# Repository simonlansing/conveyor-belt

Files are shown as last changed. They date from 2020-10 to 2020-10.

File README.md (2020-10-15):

# Miniature Conveyor Belt 

Miniature conveyor belt for simulation and having fun working with sensors and actuators, all controllable with Raspberry Pi. All sensors and actuators of the conveyor belt are connected to the GPIO pins of the Raspberry Pi via a separate circuit board. The board also contains a motor driver, a push button and three LEDs.

As simulation software [Node-RED](https://nodered.org/) is used locally on the Raspberry Pi. Based on this, the sensors and actuators could also be mapped as device shadows in the AWS IoT platform (Software follows :smile:).

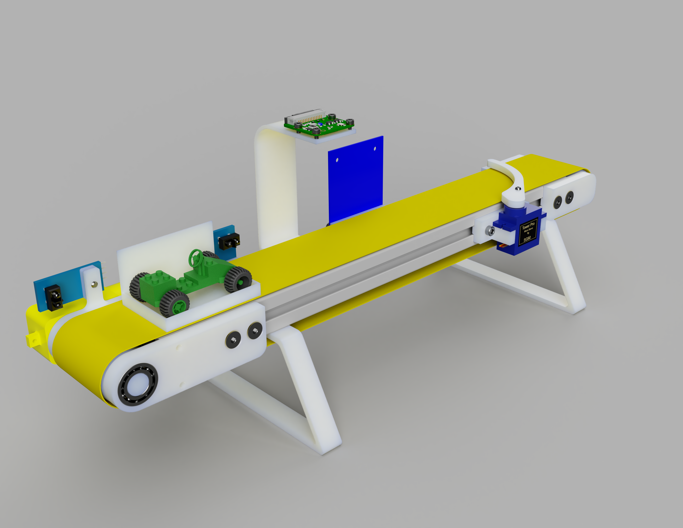
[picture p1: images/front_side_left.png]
image of front side front side

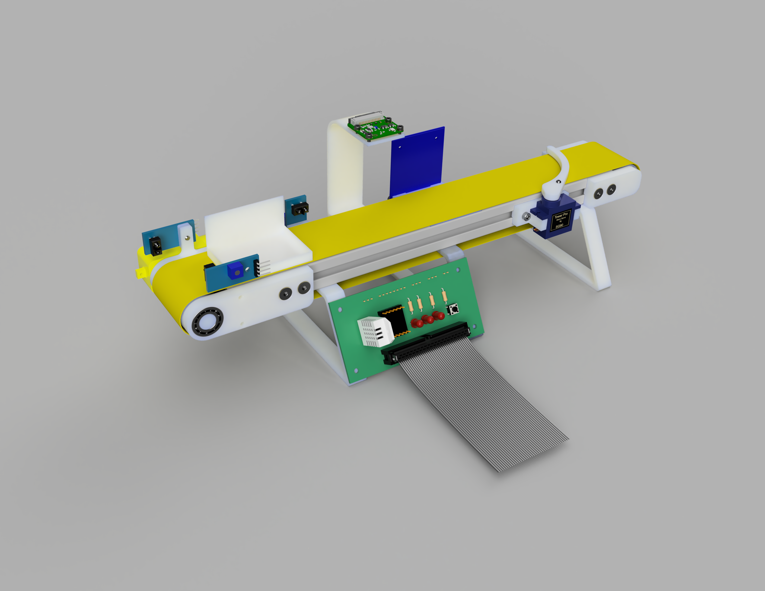
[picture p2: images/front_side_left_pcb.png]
image of front side with PCB front side with PCB

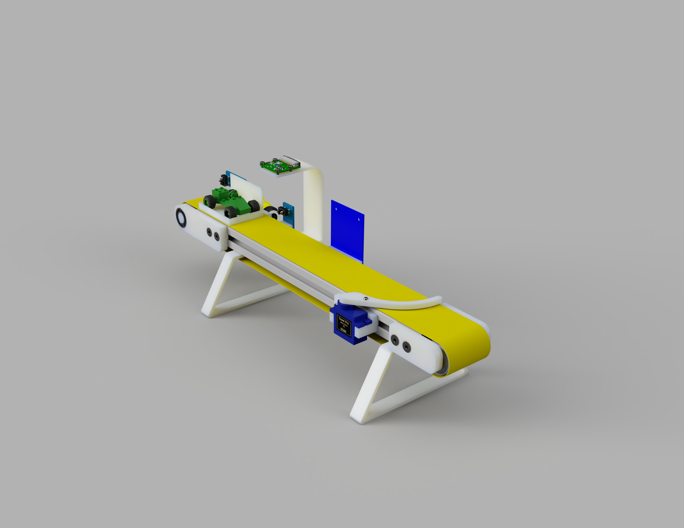
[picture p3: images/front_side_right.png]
image of front side 2 front side from other angle

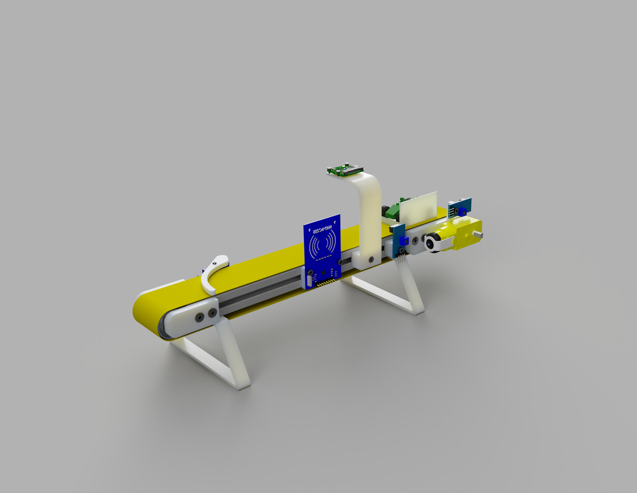
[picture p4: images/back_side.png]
image of back side back side


## Components

The following components were used and can be screwed directly to the 3D-printed parts.

### Hardware

| No. | Name | Quantity  | Notes |
| :-: | :--- | :---: | :--- |
| 1 | RFID reader RC522 | 1 | |
| 2 | IR photoelectric switch barrier TRCT5000 | 1-3 | |
| 3 | Servo motor SG90 | 1 | |
| 4 | Motor driver DRV8833 | 1 | |
| 5 | TT motor DC3V-6V | 1 | |
| 6 | Raspberry Pi Camera Module | 1 | |
| 7 | Raspberry Pi 3/4 | 1 | |
| 8 | Ball bearing 608 2RS 8x22x7 mm | 2 | deflection roll |
| 9 | Ball bearing 6800 zz 10x19x5 | 2 | drive roll |
| 10  | Aluminium profile 20mm x 40mm x 290mm | 1 | |
| 11  | Elastic band | 1 | |
| 12  | LEDs | 3 | |
| 13  | Resistors for LEDs | 3 | |
| 14  | Push button | 3 | see PCB |

### Screws

| No. | Name | Quantity  | Notes |
| :-: | :--- | :---: | :--- |
| 1 | M3 x 8 countersunk screw | 4 | |
| 2 | M3 x 10 countersunk screw | 3 | |
| 3 | M3 x 12 countersunk screw | 6 | |
| 4 | M4 x 10 countersunk screw | 24 | |
| 5 | M4 x 12 countersunk screw | 24 | |
| 6 | M3 x 5 flat headed screw | 6 | |
| 7 | M3 x 10 flat headed screw | 6 | |
| 8 | M3 x 12 flat headed screw | 6 | |
| 9 | M3 x 18 flat headed screw | 13 | |
| 10  | M3 x 25 flat headed screw | 6 | |
| 11  | M2 spacer | 6 | |

### 3D printed parts

| No. | Name | Quantity  | Notes |
| :-: | :--- | :---: | :--- |
| 1 | box | 1 | |
| 2 | camera mount | 1 | |
| 3 | deflection roll | 1 | |
| 4 | deflection roll mount | 1 | |
| 5 | deflection roll mount mirrored  | 1 | |
| 6 | drive roll | 1 | |
| 7 | foot | 2 | |
| 8 | IR sensor mount | 1-2 | one servo is mounted on the motor |
| 9 | motor mount | 1 | |
| 10  | motor mount mirrored | 1 | |
| 11  | servo lever | 1 | |
| 12  | servo mount | 1 | |

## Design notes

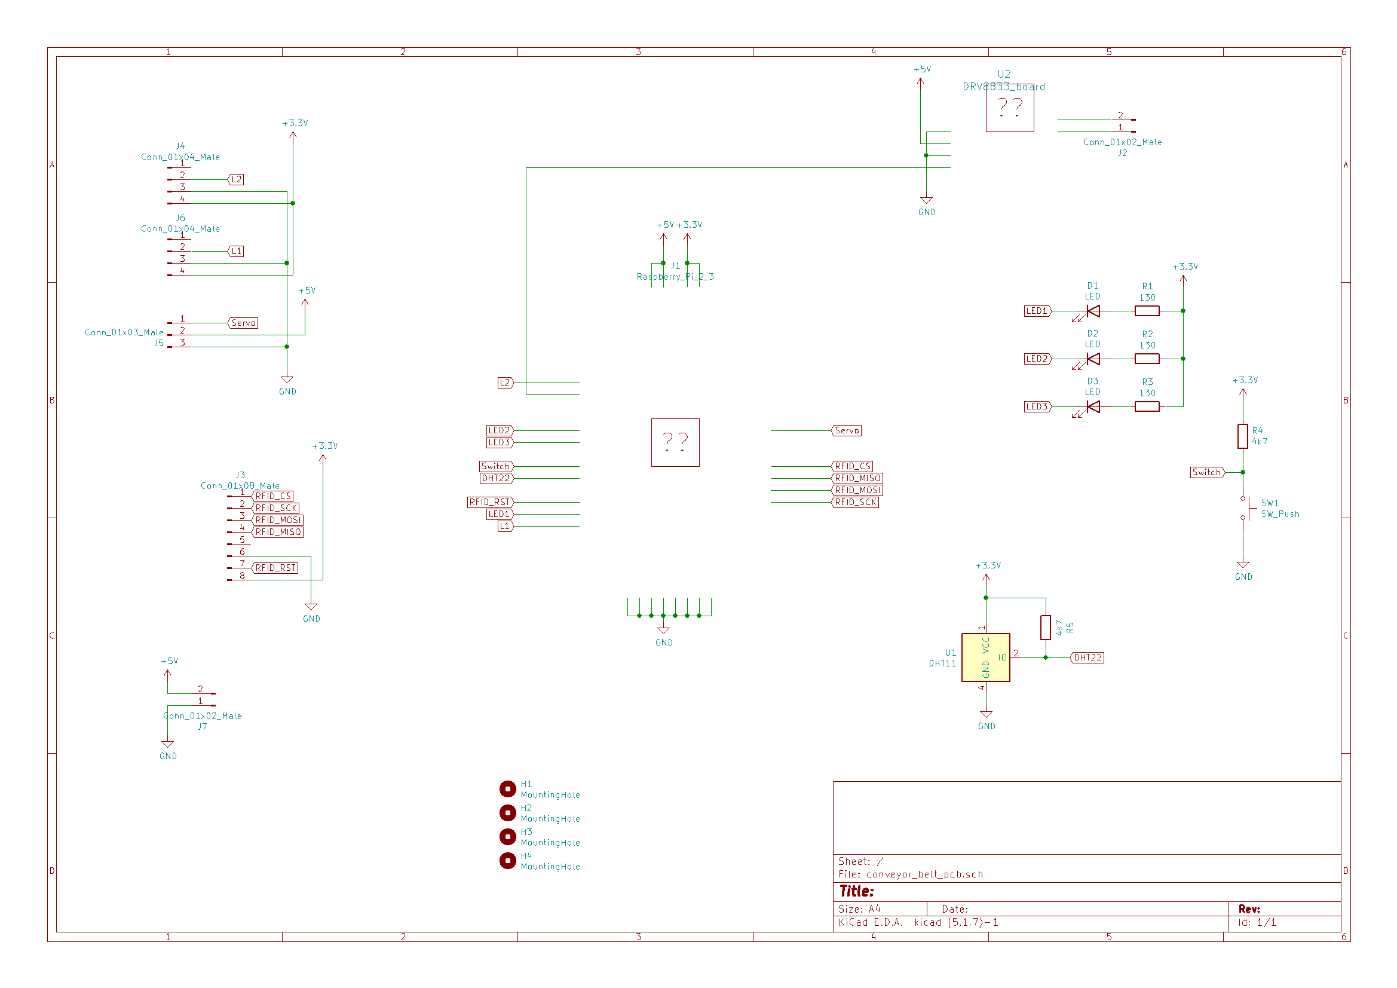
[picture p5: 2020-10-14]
images/circuit_diagram.png

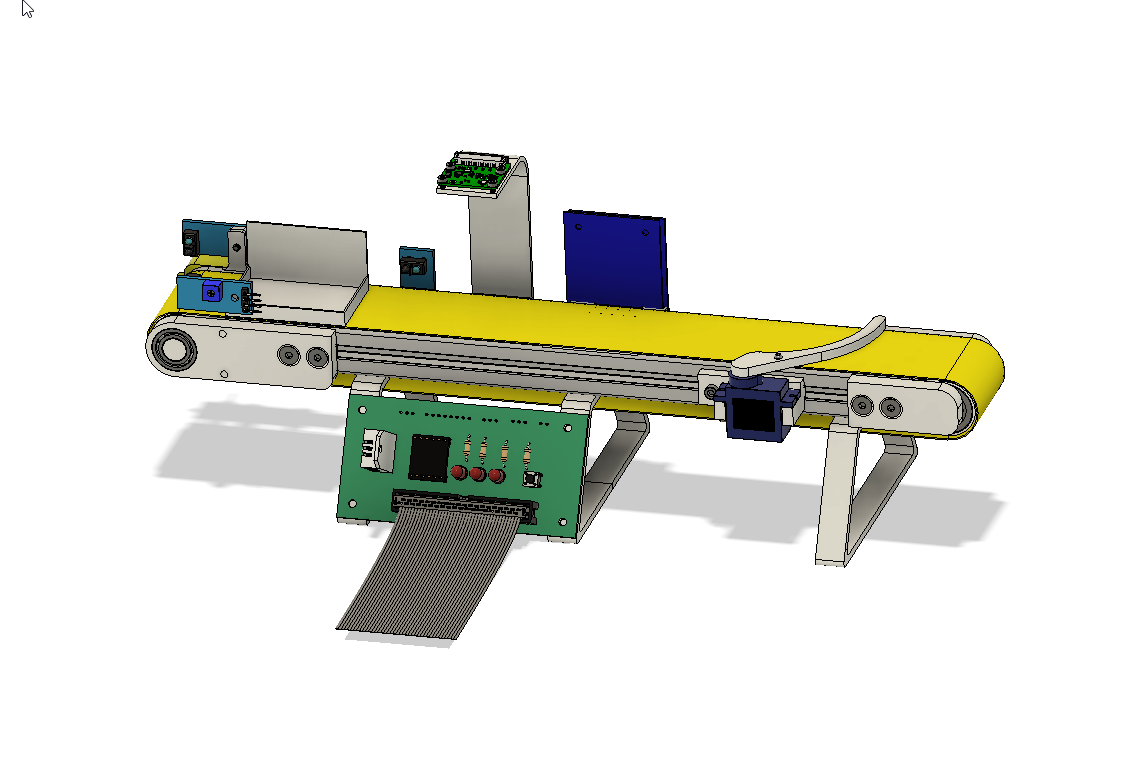
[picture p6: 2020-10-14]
images/front_pcb.png

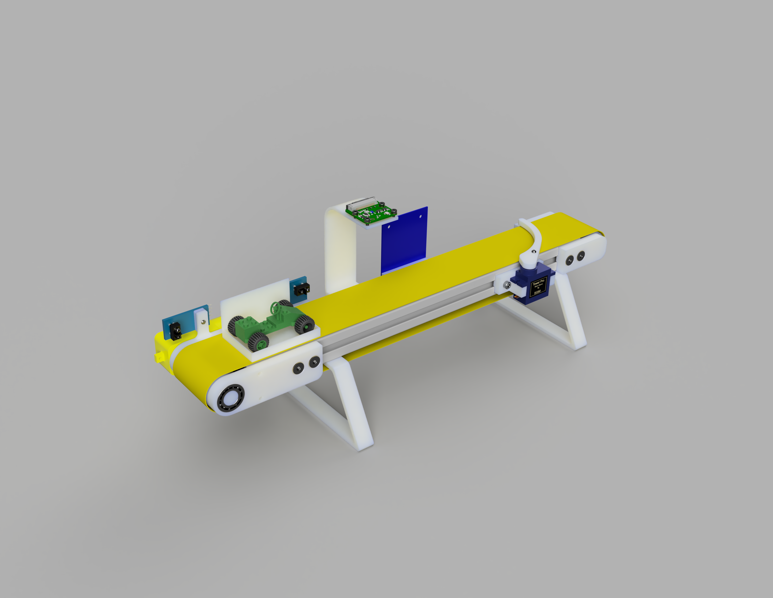
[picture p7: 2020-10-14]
images/front_side_left_2.png

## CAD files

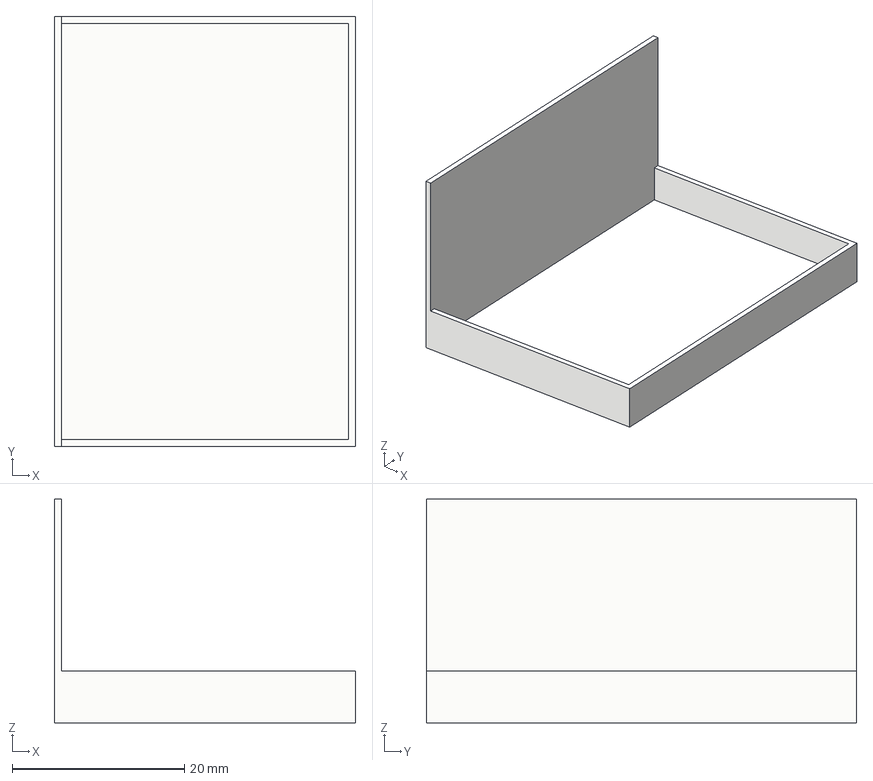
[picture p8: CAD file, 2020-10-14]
3d parts/box.step
35.0 x 50.0 x 26.0 mm

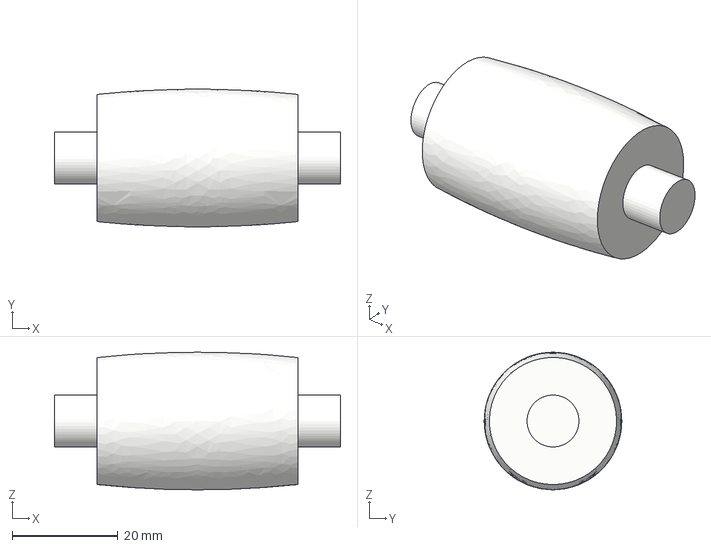
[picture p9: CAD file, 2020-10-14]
3d parts/drive_roll.step
54.0 x 26.0 x 26.0 mm

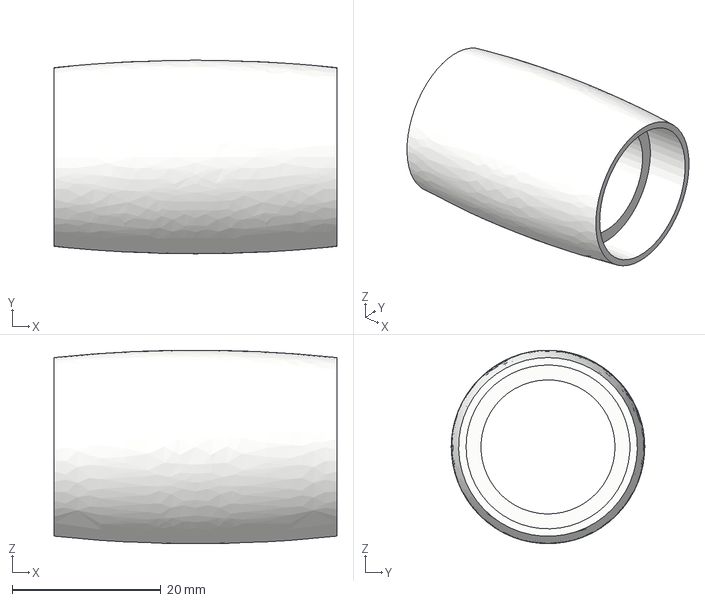
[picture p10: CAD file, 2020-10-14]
3d parts/deflection_roll.step
38.0 x 26.0 x 26.0 mm

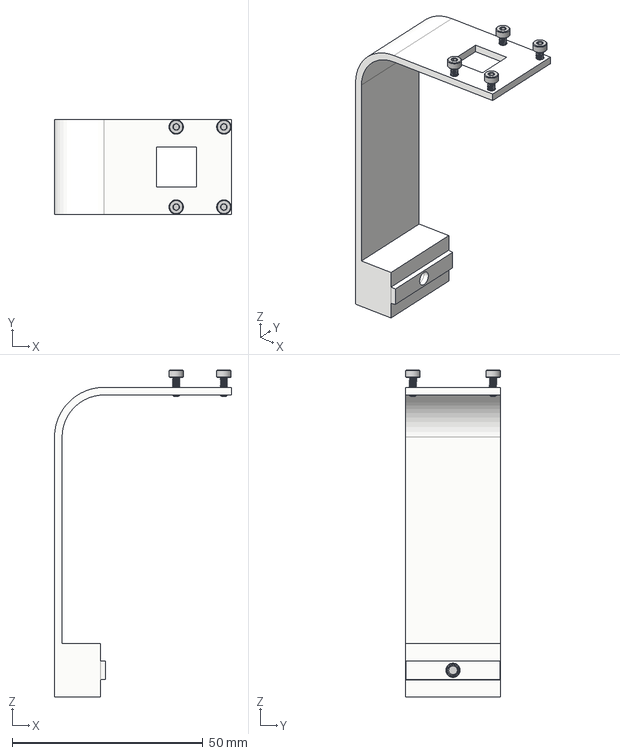
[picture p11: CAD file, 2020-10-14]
3d parts/camera_mount.step
46.4 x 25.0 x 85.7 mm
91292A005 x 4
91263A824

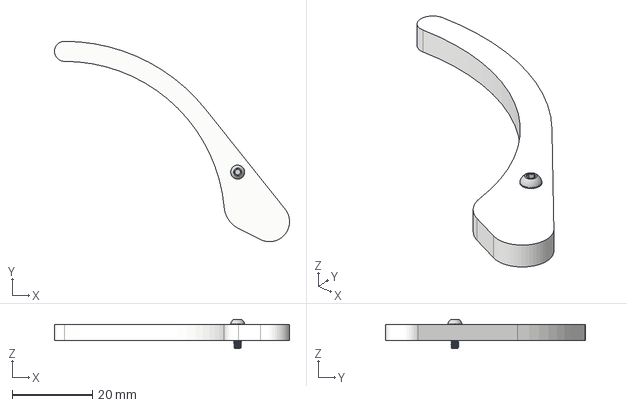
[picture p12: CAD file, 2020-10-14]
3d parts/servo_lever.step
58.6 x 50.0 x 7.30 mm

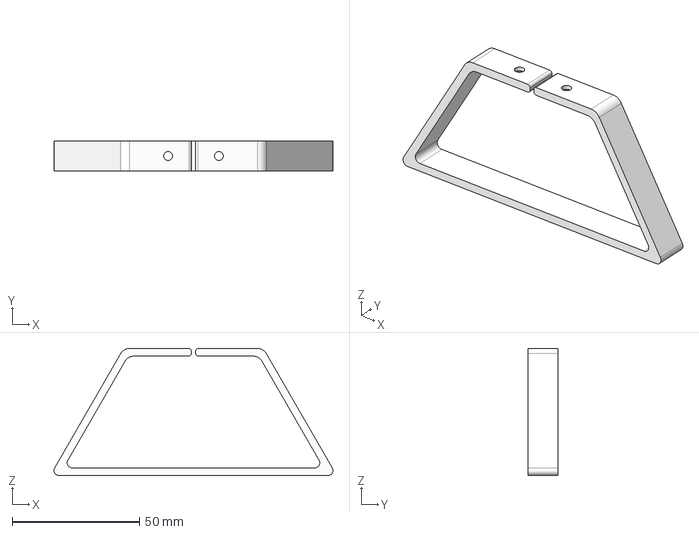
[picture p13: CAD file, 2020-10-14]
3d parts/foot.step
109.8 x 12.0 x 50.0 mm

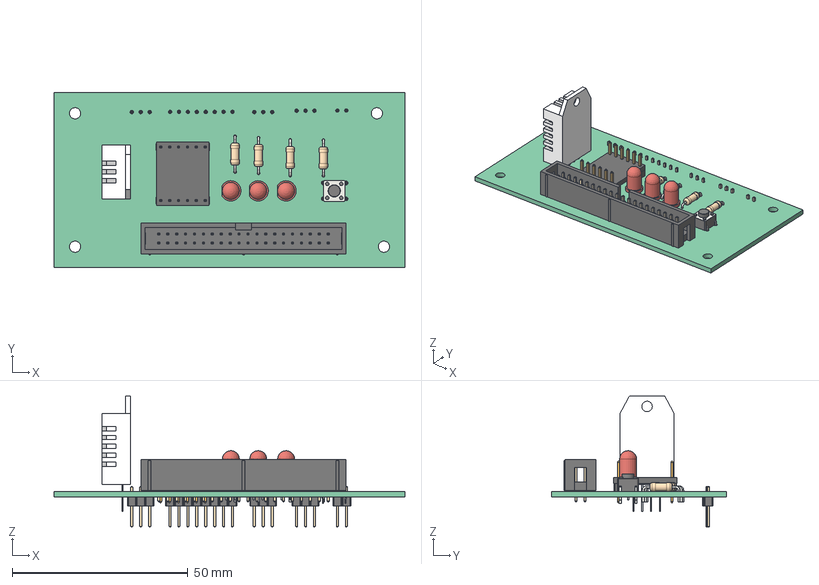
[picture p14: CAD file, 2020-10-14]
3d parts/conveyor_belt_pcb.step
100.0 x 50.0 x 37.3 mm
PCB_Sketch
U2_DRV8833_5D3FA32F
U1_DHT22_v2_5D3F8C18
SW1_SW_PUSH_6mm_h5mm_5D3F8F19
R4_R_Axial_DIN0207_L63mm_D25mm_P1016mm_Horizontal_5D3F8BE4
R3_R_Axial_DIN0207_L63mm_D25mm_P1016mm_Horizontal_5D3F8BCD
R2_R_Axial_DIN0207_L63mm_D25mm_P1016mm_Horizontal_5D3F8BB6
R1_R_Axial_DIN0207_L63mm_D25mm_P1016mm_Horizontal_5D3F8B9F
De_LED_D5.0mm_5D3F8A4F
D2_LED_D5.0mm_5D3F8A3D
D1_LED_D5.0mm_5D3F8A2B
J1_IDC_Header_2x20_P254mm_Vertical_5D3F6757
J6_PinHeader_1x03_P254mm_Vertical_5D3F8B88
J5_PinHeader_1x03_P254mm_Vertical_5D3F8B71
J4_PinHeader_1x03_P254mm_Vertical_5D3F8B5A
J3_PinHeader_1x08_P254mm_Vertical_5D3F8B43
J2_PinHeader_1x02_P254mm_Vertical_5D3F904C

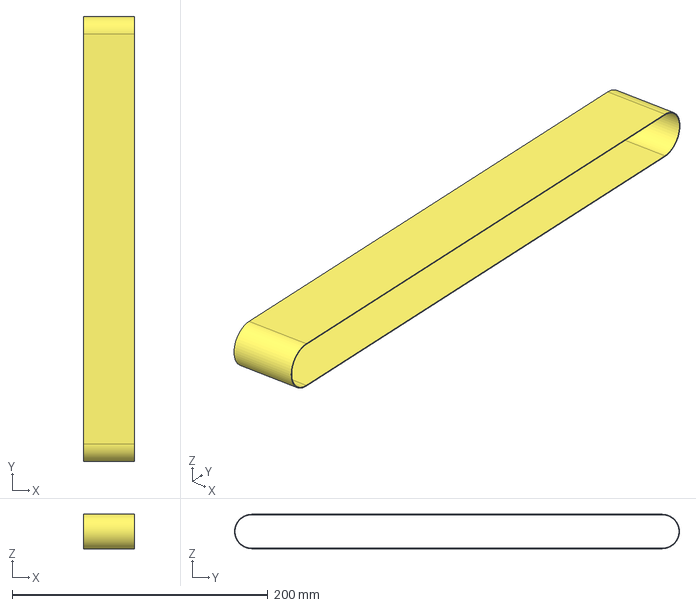
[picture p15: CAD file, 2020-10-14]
3d parts/elastic_band.step
40.0 x 348.0 x 27.0 mm

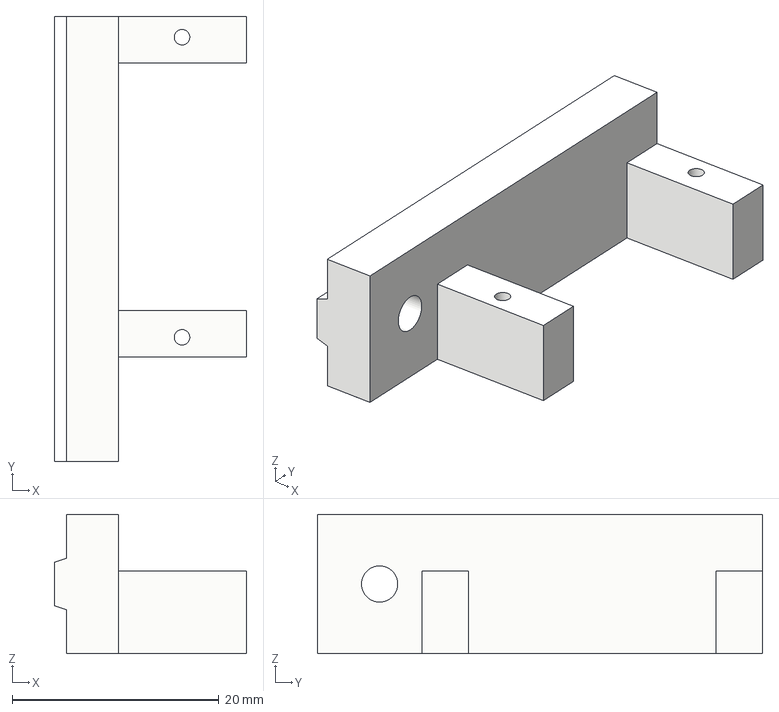
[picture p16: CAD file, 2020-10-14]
3d parts/servo_mount.step
18.6 x 43.0 x 13.5 mm

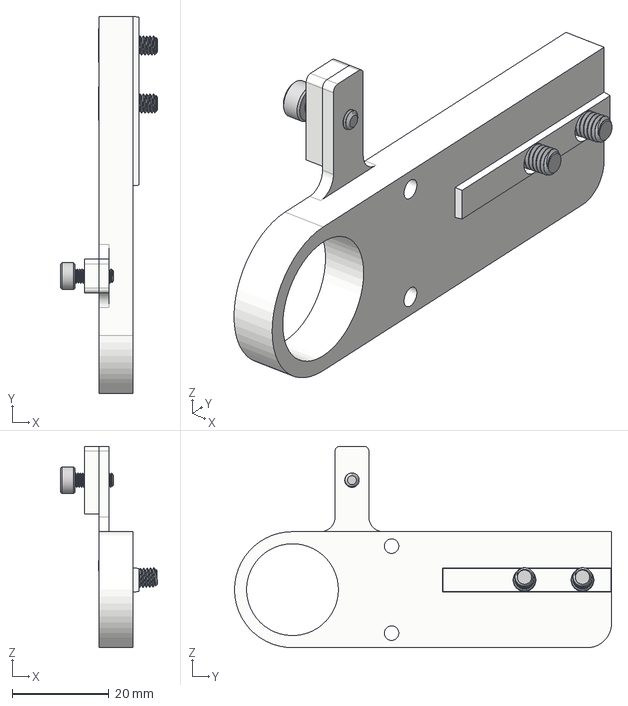
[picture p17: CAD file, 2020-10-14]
3d parts/motor_mount.step
20.1 x 78.0 x 41.7 mm
95263A122
91263A829 x 2

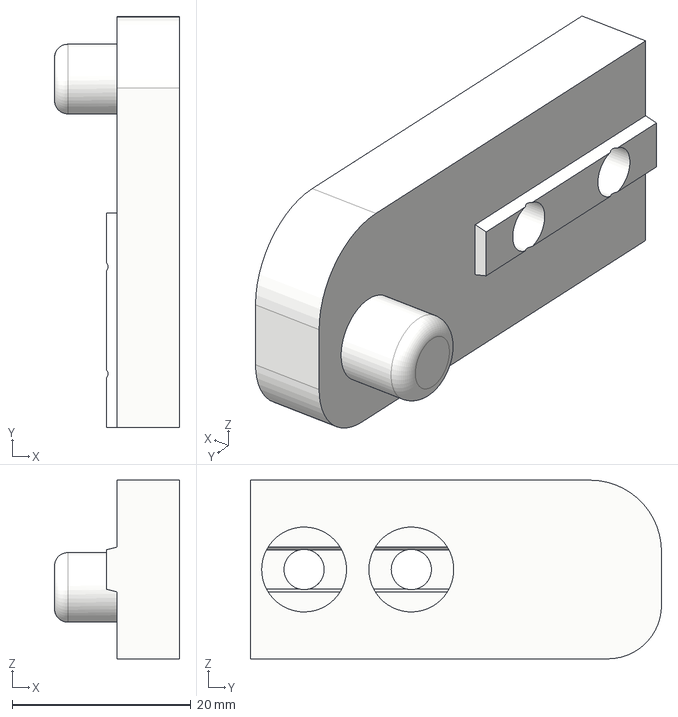
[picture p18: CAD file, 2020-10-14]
3d parts/deflection_roll_mount.step
14.0 x 46.0 x 20.0 mm

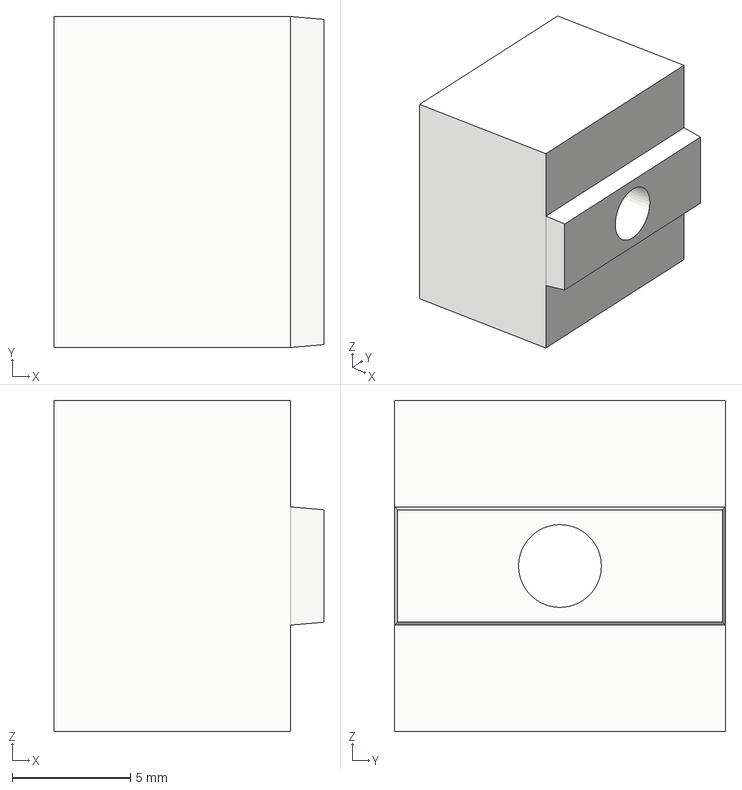
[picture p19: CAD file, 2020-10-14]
3d parts/ir_sensor_mount.step
11.4 x 14.0 x 14.0 mm

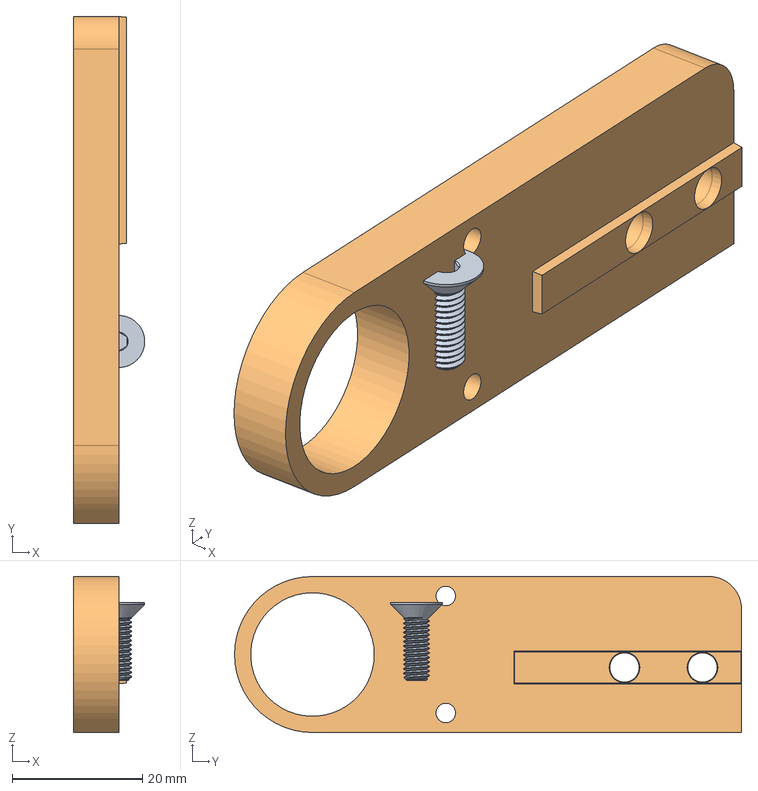
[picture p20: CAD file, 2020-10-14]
3d parts/motor_mount_mirrored.step
11.0 x 78.0 x 24.0 mm

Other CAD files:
3d parts/deflection_roll_mount_mirrored.step

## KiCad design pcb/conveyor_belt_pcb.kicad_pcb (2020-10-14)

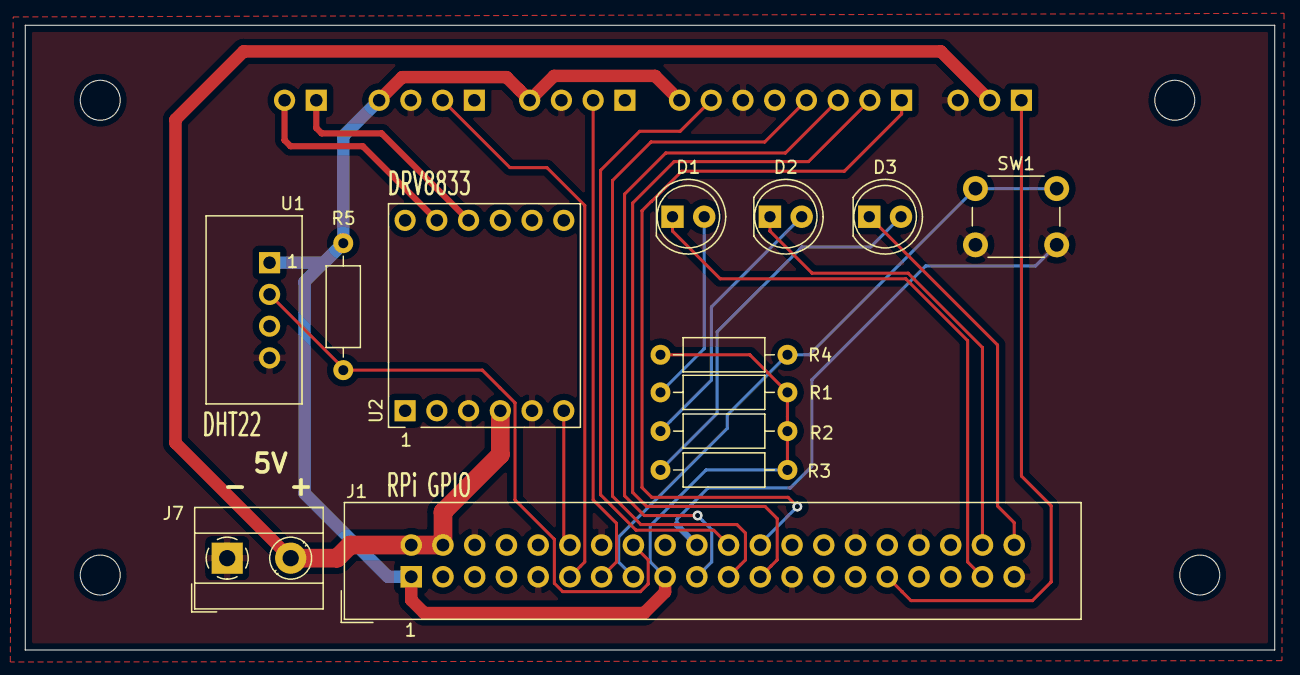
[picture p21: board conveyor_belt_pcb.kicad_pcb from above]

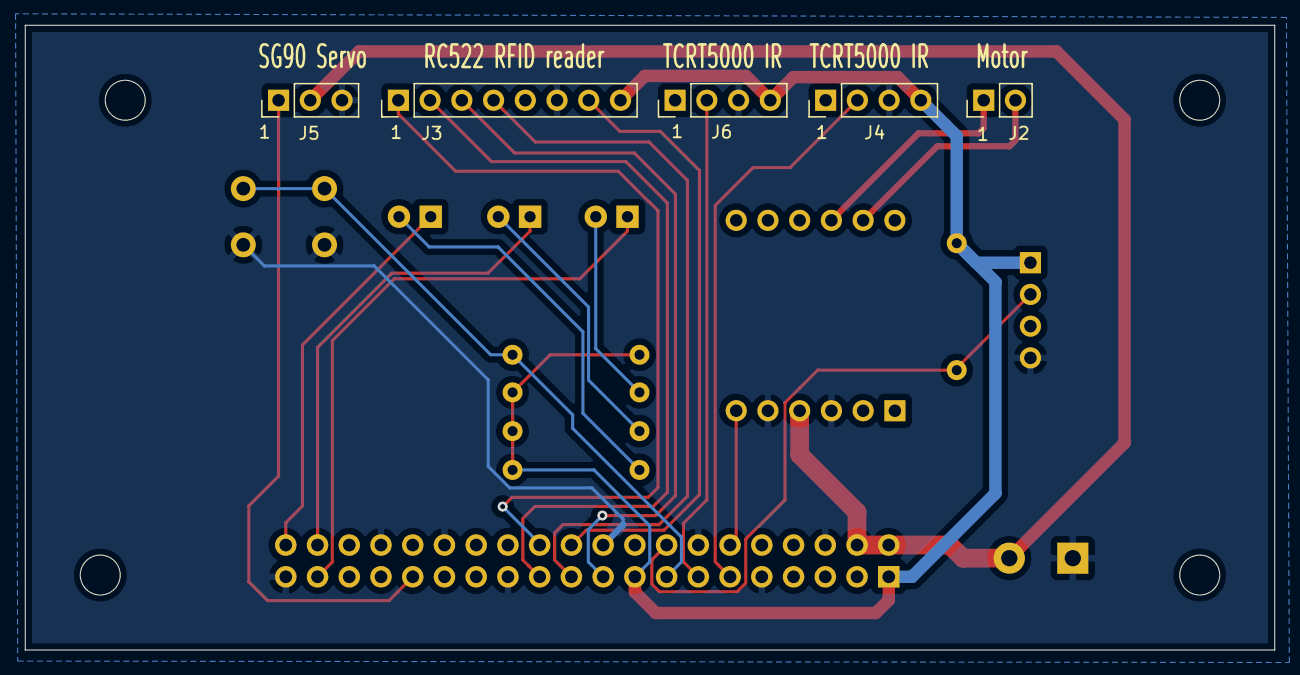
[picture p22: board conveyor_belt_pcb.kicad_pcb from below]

Board: 2 copper layers, 100.0 x 50.0 mm, 22 parts (5 on the bottom side), 22 nets.

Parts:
D1, D2, D3: LED; LED_D5.0mm
H1, H2, H3, H4: MountingHole; MountingHole_3.2mm_M3
J1: Raspberry_Pi_2_3; IDC-Header_2x20_P2.54mm_Vertical
J2: Conn_01x02_Male; PinHeader_1x02_P2.54mm_Vertical
J3: Conn_01x08_Male; PinHeader_1x08_P2.54mm_Vertical
J4, J6: Conn_01x04_Male; PinHeader_1x04_P2.54mm_Vertical
J5: Conn_01x03_Male; PinHeader_1x03_P2.54mm_Vertical
J7: Conn_01x02_Male; TerminalBlock_MetzConnect_Type101_RT01602HBWC_1x02_P5.08mm_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
R1, R2, R3: 130; R_Axial_DIN0207_L6.3mm_D2.5mm_P10.16mm_Horizontal
R4, R5: 4k7; R_Axial_DIN0207_L6.3mm_D2.5mm_P10.16mm_Horizontal
SW1: SW_Push; SW_PUSH_6mm_H5mm
U1: DHT11; DHT22
U2: DRV8833_board; DRV8833_BOARD_2x06_P2.54mm_Vertical

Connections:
+3V3: J1.1, J1.17, J3.8, J4.4, J6.4, R1.1, R2.1, R3.1, R4.2, R5.2, U1.1
+5V: J1.2, J1.4, J5.2, J7.2, U2.4
DHT22: J1.16, R5.1, U1.2
GND: J1.6, J1.9, J1.14, J1.20, J1.25, J1.30, J1.34, J1.39, J3.6, J4.3, J5.3, J6.3, J7.1, SW1.2, U1.4, U2.3, U2.5
L1: J1.13, J6.2
L2: J1.11, J4.2
LED1: D1.1, J1.37
LED2: D2.1, J1.38
LED3: D3.1, J1.40
unnamed: D1.2, R1.2
unnamed: D2.2, R2.2
unnamed: D3.2, R3.2
unnamed: J1.12, U2.6
unnamed: J2.1, U2.10
unnamed: J2.2, U2.11
RFID_CS: J1.24, J3.1
RFID_MISO: J1.21, J3.4
RFID_MOSI: J1.19, J3.3
RFID_RST: J1.22, J3.7
RFID_SCK: J1.23, J3.2
Servo: J1.31, J5.1
Switch: J1.15, R4.1, SW1.1
